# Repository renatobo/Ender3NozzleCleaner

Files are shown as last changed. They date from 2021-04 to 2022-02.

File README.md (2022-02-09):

# Ender3NozzleCleaner
Easy and automatic nozzle cleaning for an Ender 3 Pro with an inexpensive brush.

PETG is quite stringy and having strings of filament on your first layer is quite annoying. To avoid babysitting each print, I looked at a couple of designs on thingiverse but none really worked well for an Ender 3 Pro.

## What you need

* Cheap brass brush - in this design I used a [sub-1$ one from Harbor Freight](https://www.harborfreight.com/brass-detail-brush-69524.html)
* 2 or 3 M1.7 screws (or equivalent very small and short screws)
* T-Nut (you can 3d print [this M3 Tnut](https://www.thingiverse.com/thing:3050607) )
* Brush support

## How-to

* 3d print brush support (both STL and Fusion360 files are provided)
* 3d print Tnuts (or buy/reuse other ones)
* Cut away the brush handle: keep the part where the brass brush is
* Extend limits of your printer: in my case I found that I can safely extend X to 248 mm
* Write a sequence of Gcode commands that moves the head back and forth (see examples at [nozzle_clean.gcode](nozzle_clean.gcode) and [g12_macro_klipper.cfg](g12_macro_klipper.cfg) )

## End result

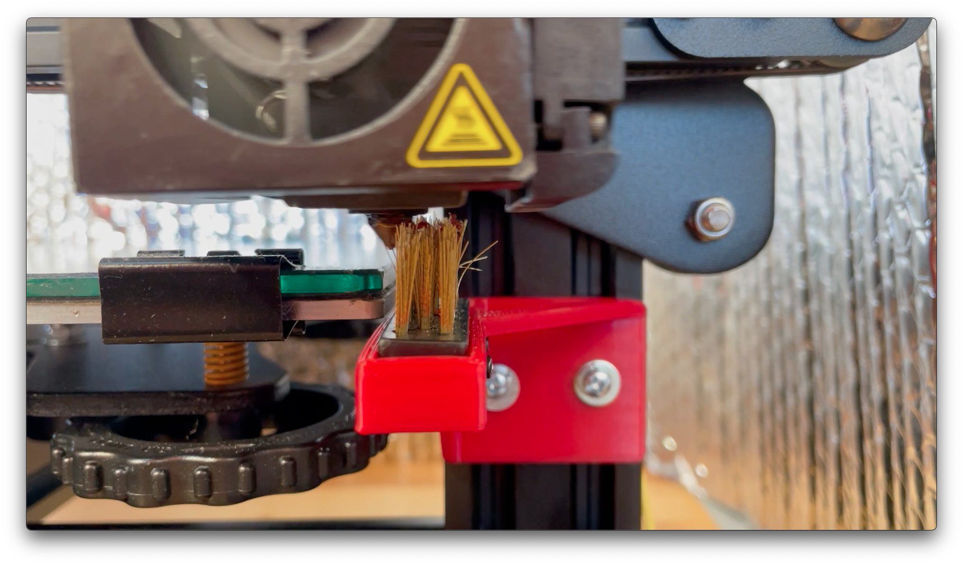
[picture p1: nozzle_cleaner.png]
nozzle cleaner


In action:

* [Overall](https://youtu.be/dVcODpnYj88)
* [Closeup](https://youtu.be/zQN17WtxQjo)

## Tip: Klipper Macro for G12

A good option is to define the cleaning code as G12 and use a macro in klipper.
See code at [g12_macro_klipper.cfg](g12_macro_klipper.cfg)

## Tip: mounting the support
The support it works best when the display is removed. If the display is not removed, you need to offset Z commands upwards in the examples provided.

## Tip: extending printer bed size

I use Klipper and I simply modified the `printer.cfg` file to account for a larger X dimension

```
[stepper_x]
#...
position_endstop: 0
position_max: 248
```

Do not modify your slicer, it might think there is more bed than there is

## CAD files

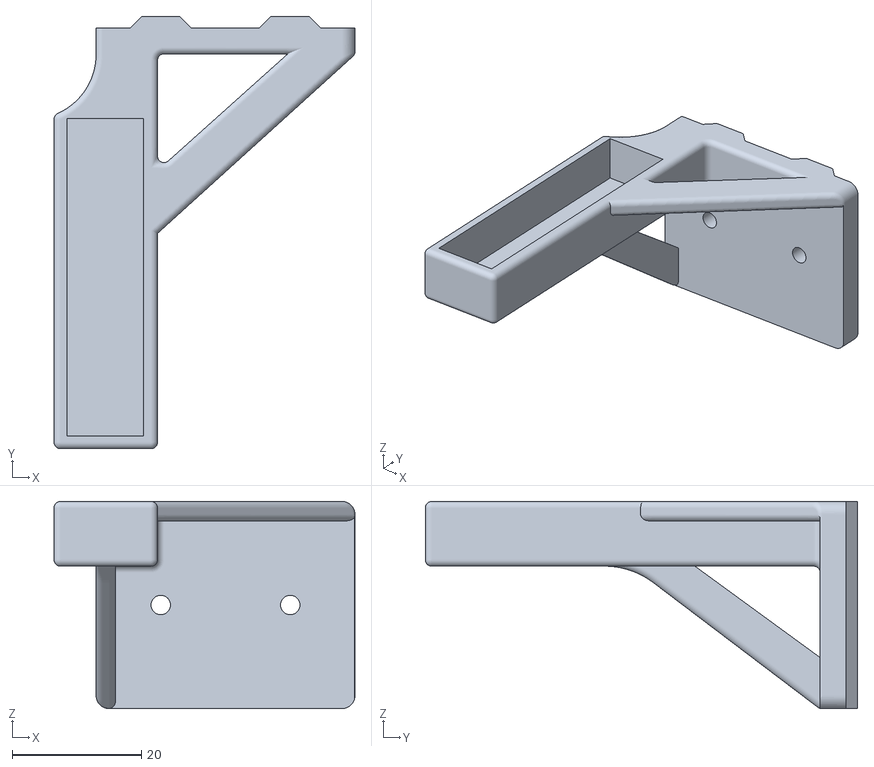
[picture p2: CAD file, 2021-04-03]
Nozzle brush cleaner v4.stl
46.5 x 66.8 x 32.0

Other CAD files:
Nozzle brush cleaner v4.f3d

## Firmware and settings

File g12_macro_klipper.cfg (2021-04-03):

# This macro can be used in slicers that have the option to clean the nozzle to simulate Marlin's behavior
# It does not accept parameters that a regular G12 would use
#
# You should customize variables 
# x_nozzleclean_position -> this is defined as the end of the X axis
# hotend_temperature -> you need to heat up the hotend
#
# You could customize
# speed_list -> a list of speeds (slowest .. to fastest) iterating the procedure
# the number of iterations of each run: increase or decrease occurences of range(3) 


[gcode_macro G12]
gcode:
   # Right of the cleaning strip/brush
   {% set x_nozzleclean_position = (printer.toolhead.axis_maximum.x|int) %}
   # Set your melting temperature for plastic on nozzle
   {% set hotend_temperature  = 245 %}
   # A slow, medium, fast set of speeds. Enter them in order, you can add more but first and last are used below
   {% set speed_list = ['500','2500','5000'] %}
   M117 Clean Nozzle
   {% if printer.idle_timeout.state == "Printing" %}
    SAVE_GCODE_STATE NAME=clean_nozzle
   {% else %}
    G28 # home
    M104 S{ hotend_temperature } # heat up
   {% endif %}

    G90 ; use absolute positioning
    G0 X{ x_nozzleclean_position - 30 } Y0 Z20 F{ speed_list|last }# move towards cleaning location, 20mm higher than bed
    G0 X{ x_nozzleclean_position } F{ speed_list|first }# slow down since we are at the end of the space
    M106 S255# cool filament drooling from piece to ease detach

   {% if printer.idle_timeout.state != "Printing" %}
    M109 S{ hotend_temperature } # wait for extruder to be 245
   {% endif %}

    M106 S0 # turn off fan,  begin cleaning back and forth, descending 1 mm at a time
    G10 # firmware retraction to alleviate pressure
    G91 # relative positions

    # get rid of longer part right now, diving down, then going left to the middle, up and down, then up right
    G0 Z-20 F{ speed_list|last } # fast speed
    G0 X-10#

    {% for i in range(3) %}
     G0 X+1 Z+5;
     G0 X-1 Z+5;
     G0 X+1 Z-5;
     G0 X-1 Z-5;
    {% endfor %}

   G0 X+10 Z+10 # go back
   G0 Z-1 # decrease 1 Z -> adjust here the starting point of the nozzle

   {% for speed in speed_list %}
    G0 F{ speed } # change speed
    # down
     {% for i in range(3) %}
     G0 X-20 Z-1
     G0 X+20 Z-1
    {% endfor %}
    # a few extra runs
     {% for i in range(3) %}
     G0 X-20
     G0 X+20
     {% endfor %}
    #up
     {% for i in range(3) %}
      G0 X-20 Z+1
      G0 X+20 Z+1
     {% endfor %}
   {% endfor %}

   G0 Z+10;
   G90; back to absolute position

   {% if printer.idle_timeout.state == "Printing" %}
    RESTORE_GCODE_STATE NAME=clean_nozzle
   {% else %}
    G0 X0 Y0 Z10 F{ speed_list|last } # back to home
    M18 # turn off motors
    TURN_OFF_HEATERS
   {% endif %}
   
